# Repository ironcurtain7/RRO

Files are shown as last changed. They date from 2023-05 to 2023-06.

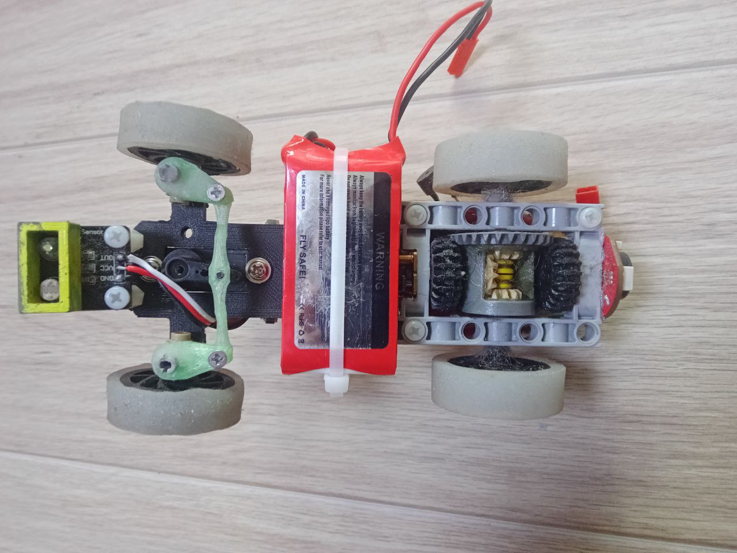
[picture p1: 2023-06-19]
v-photos/5.jpg

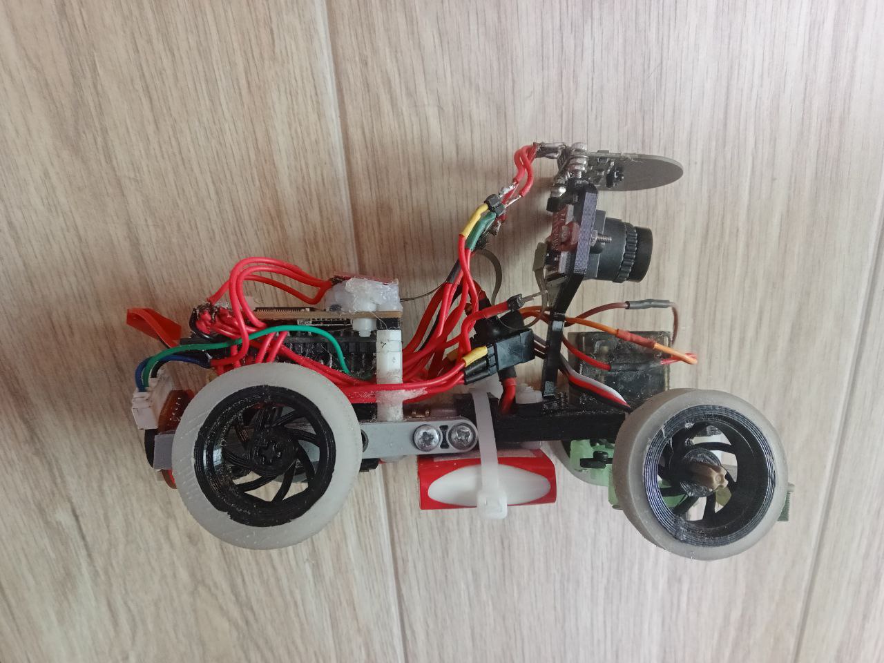
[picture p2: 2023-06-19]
v-photos/3.jpg

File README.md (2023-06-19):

Команда Роботикс (Robotx). Описание робота для соревновний FutureEngineers 2023.

Файловая структура:

models - модели для 3d печати.

t-photos - фото команды.

v-photos - фото транспортного средства.

schemes - схема электронных компонентов.

src - исходный код программ.

Робот был сделан на основе самостоятельно разработанного и напечатанного на 3D-принтере шасси, а так же элементов LEGO. 3D модели для печати находятся в папке models. Вариант самостоятельной разработки шасси был выбран по двум причинам:

- возможность сделать шасси нужной конфигурации для оптимального расположения электронных и механических компонентов робота
- уменьшения массы робота и улучшенния маневренности по сравнению с готовыми радиоуправляемыми шасси
  
Система перемещения робота:

Автомобиль состоит из: двусоставной рамы(из напечатанных деталей и частей конструктора LEGO, крепления мотора, крепления камеры, крепления датчиков, дисков колес и силиконовых покрышек.(car_frame.stl, motor_mount.stl, camera_mount.stl, sensor_mount.stl, rim.stl, wheels1.stl, wheels2.stl)

Электронная составляющая робота: ESP32(главный микроконтроллер), OpenMV H7(второстепенный контроллер для обработки изображения с камеры), стабилизатор напряжения mini360, двигатель MR12-020, драйвер двигателя ta6586, инфракрасный дальномер OPT3101, сервопривод Tower Pro MG90S, а питание идет от аккамулятора LiPo 2s (7.4V) 460mAh.

Используемые датчики: Инфракрасный дальномер OPT3101 (для определения расстояния до стены), фоторезистор со светодиодной подсветкой (для определения цвета линий).

Подключение всех электронных эллементов происходит через провода в силиконовой оболочке т. к. пайка дает лучше соеденение чем стандартные коннекторы.

Для крепления компонентов много где используются пластиковые стойки и пластиковые винты с гайками.

Робот включается с помощью выключателя на кабеле к батарее. Запускаются оба контроллера. После этого ESP32 инициализирует драйвер/основной двигатель, сервопривод, датчик расстояния и датчик линии. После этого издается звуковой сигнал и робот ждет нажатия на кнопку старта.

Логика работы программы:

Квалификационный заезд (робот устанавливается на поле строго вдоль бортов, основная программа начинает работать после нажатия кнопки старта):

1. Робот двигается вперед строго прямо до нахождения синей/оранжевой полосы с помощью датчика яркости света
2. Если найдена синяя/оранжевая полоса, то в зависимости от цвета линии, робот едет с поворотом колес налево/направо на нужный угол необходимое количество времени таким образом, чтобы подъехать к перпендикулярной стене на расстояние примерно 20см и встать вдоль нее. Угол и время проезда подбирается опытным путем.
3. Затем запускается блок программы езды вдоль внешней стены полигона с помощью дальномеров и PID-регулятора. Робот едет на расстоянии 20см от внешней стены. Т.е. если первый поворот был налево и внешняя стенка справа, то едем по правому дальномеру. И наоборот.
4. Во время езды вдоль стены анализируем показания датчика яркости и определяем наезд на синюю/оранжевую линию.
5. Если наехали на синюю/оранжевую линию, то робот поворачивает колеса на нужный угол налево/направо и проезжает неободимое расстояние для того, чтобы подъехать к перпендикулярной стене на расстояние 20см и встать вдоль нее. Угол и расстояние проезда подбирается опытным путем.
Затем алгоритм повторяется с п.3 до тех пор пока количество поворотов не достигнет 12.
После проезда двенадцатого поворота проезжаем заранее подобранное время с заранее подобранным углом поворота колес и останавливаемся.

Финальный заезд (робот устанавливается на поле строго вдоль бортов, основная программа начинает работать после нажатия кнопки старта):

1. Двигается вперед строго прямо до нахождения синей/оранжевой полосы с помощью датчика яркости света. Если перед роботом стоит кубик, то объезжаем его(алгоритм объезда описан в п.3).
2. Если найдена синяя/оранжевая полоса, то в зависимости от цвета линии, робот едет с поворотом колес налево/направо на нужный угол необходимое количество времени таким образом, чтобы подъехать к перпендикулярной стене на расстояние примерно 50см и встать вдоль нее. Угол и время проезда подбирается опытным путем.
3. Затем запускается блок программы езды вдоль внешней стены полигона с помощью дальномеров и PID-регулятора. Робот едет на расстоянии 50см от внешней стены. Т.е. если первый поворот был налево и внешняя стенка справа, то едем по правому дальномеру. И наоборот.
Во время езды вдоль стены анализируем показания с контроллера OpenMV H7. Если контроллер OpenMV находит препятствие, то передает данные о цвете и координатах препятствия на контроллер ESP32. ESP32 направляет робота на препятсвие (постоянно получая данные с OpenMV о координатах препятсвия) для того, чтобы выровнять робота относительно препятствия. Т.е. препятсвие будет находиться строго перед роботом. Далее робот делает маневр объезда препятсвия в зависимости от цвета слева или справа. Объезд (углы поворота колес и время проезда) настраивается опытным путем. После объезда робот снова начинает ехать вдоль внешней стены.
4. Одновременно с получением данных с OpenMV, контроллер ESP32 анализирует показания датчика яркости и определяет наезд на синюю/оранжевую линию.
5. Если наехали на синюю/оранжевую линию, то робот поворачивает колеса на нужный угол налево/направо и проезжает неободимое расстояние для того, чтобы подъехать к перпендикулярной стене на расстояние 20см и встать вдоль нее. Угол и расстояние проезда подбирается опытным путем.
Затем алгоритм повторяется с п.3 до тех пор пока количество поворотов не достигнет 12.
После проезда двенадцатого поворота проезжаем заранее подобранное время с заранее подобранным углом поворота колес и останавливаемся.

Программа для ESP32 написана на языке C++, для OpenMV - на языке python. Исходный код находится в папке src.

qual.cpp - программа для квалификационного заезда на ESP32

final.cpp - программа для финального заезда на ESP32

main.py - программа для контроллера OpenMV H7

Программы для ESP32 используют стандартные библиотеки из фреймворка PlatformIO, компилируются и загружаются в контроллер в среде Microsoft Visual Studio Code. Программа для OpenMV H7 загружается в контроллер с помощью стандартной среды разработки от контроллеров OpenMV. (Скачать можно по ссылке https://openmv.io/pages/download)

Программы для квалификационного и финального заездов во многом схожи и состоят из таких блоков:

Блок добавления библиотек, определения переменных и создание объектов для управления сервоприводом, основным двигателем и дальномерами.

Функция Setup(). Инициализация дальномеров. Указание его режима и параметров работы, а так же инициализация Serial порта, драйвера, сервопривода, датчика линии и т.д.

Функция start(). Проезд до первого поворота, определение направления поворота и непосредственно выполнение поворота.

Функция speek(). Отладочная функция которая издает звуковые сигналы в зависимости от выбранного времени звучания при помощи входного параметра функции

Функция ReadUZ(). Считывание расстояние с датчика в зависимости от выбранного датчика при помощи входного параметра функции(возвращает растояние до стены, и используется в функциях ride(), turn())

Функция ride(). Езда вдоль стены с заданным расстоянием. В программе final.cpp в данной функции еще и объезд светофоров в зависимости от цвета слева/справа.

Функция turn(). Поворот под прямым углом в зависимости от цвета линии налево/направо.

Функция loop(). Основной цикл программы. В ней вызываются функции для езды робота.

В программе для контроллера OpenMV H7 следующие блоки:

Импорт библиотек и определение переменных

Определение порогов цветов в цветовой модели LAB для определения объектов красного и зеленого цветов.

Настройка Serial порта и режима работы камеры

Блок определения красных объектов в необходимой области видимости (ROI) и передача цвета и х-координаты и высоты светофора в контроллер ESP32 по Serial порту.
Блок определения зеленых объектов в необходимой области видимости (ROI) и передача цвета и х-координаты и высоты светофора в контроллер ESP32 по Serial порту.

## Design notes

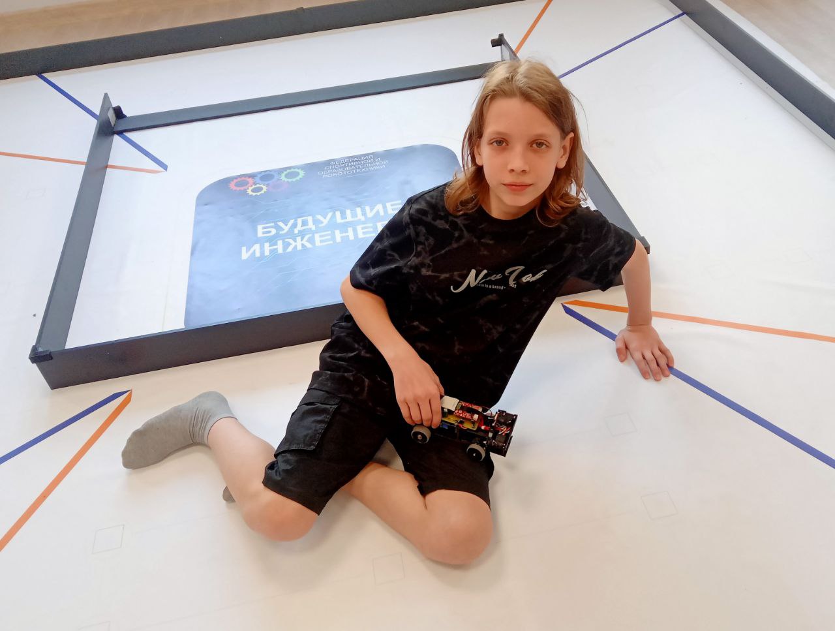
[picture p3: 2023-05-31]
t-photos/funny.jpg

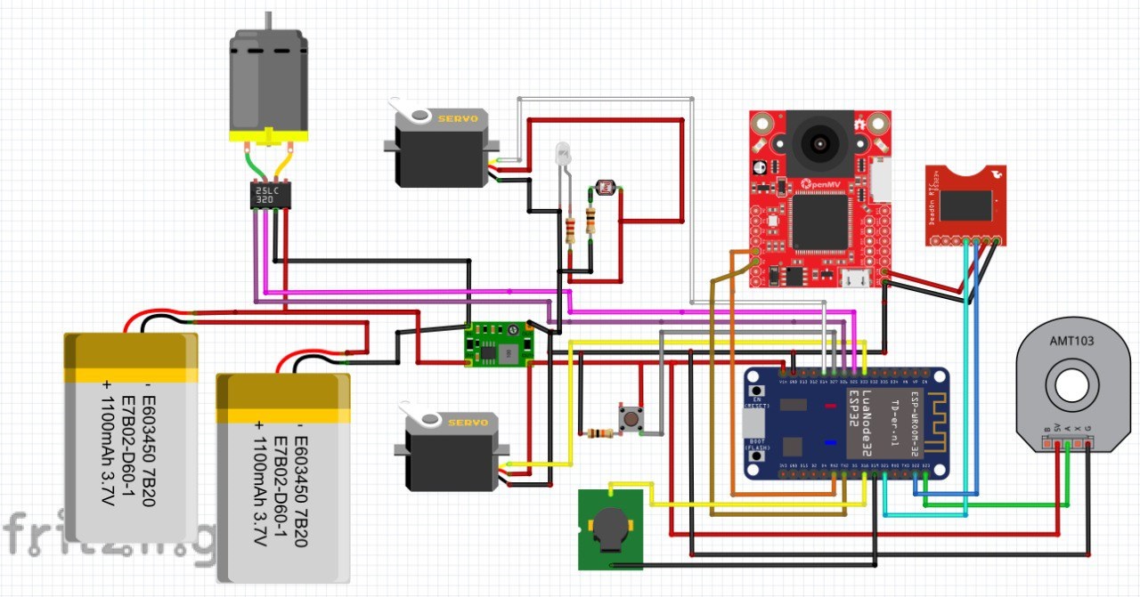
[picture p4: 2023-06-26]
schemes/image.jpg

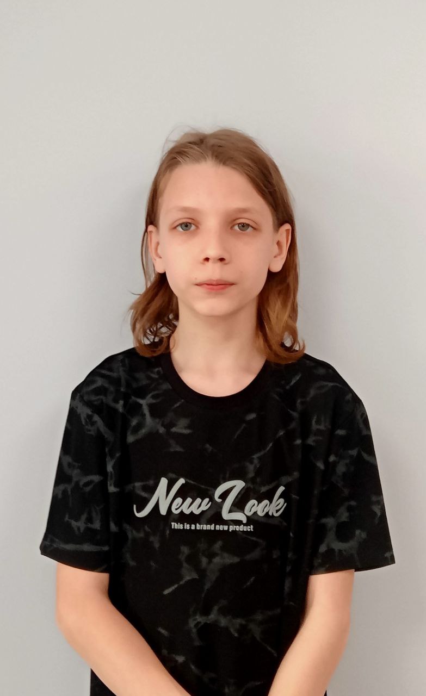
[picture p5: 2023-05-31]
t-photos/official.jpg

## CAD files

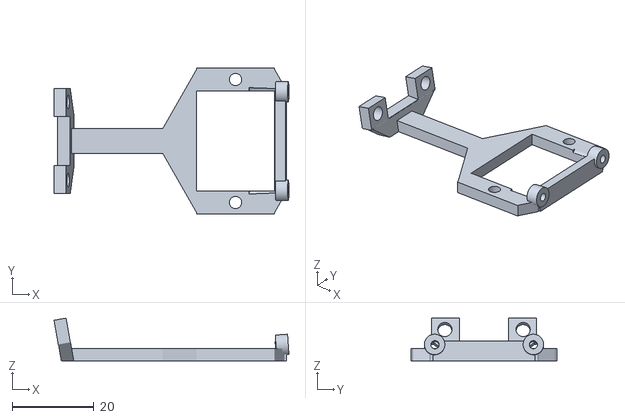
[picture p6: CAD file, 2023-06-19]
models/camera_and_sensor_stand.stl
57.3 x 35.5 x 10.4

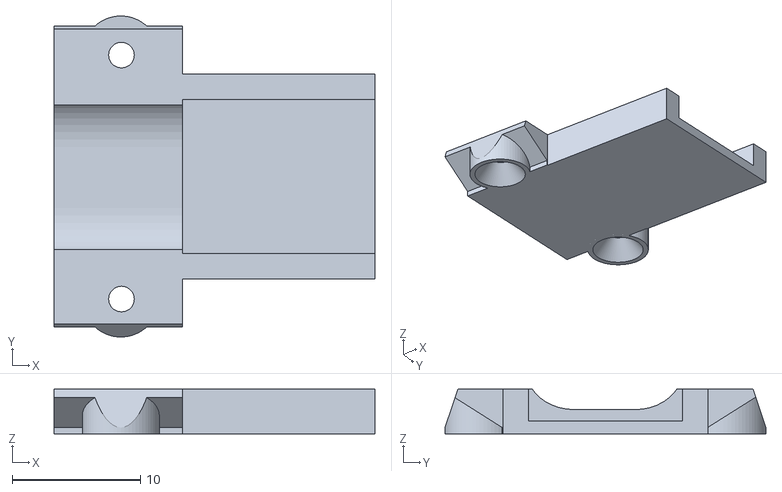
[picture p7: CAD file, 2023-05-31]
models/motor_cover.stl
25.0 x 25.0 x 3.50

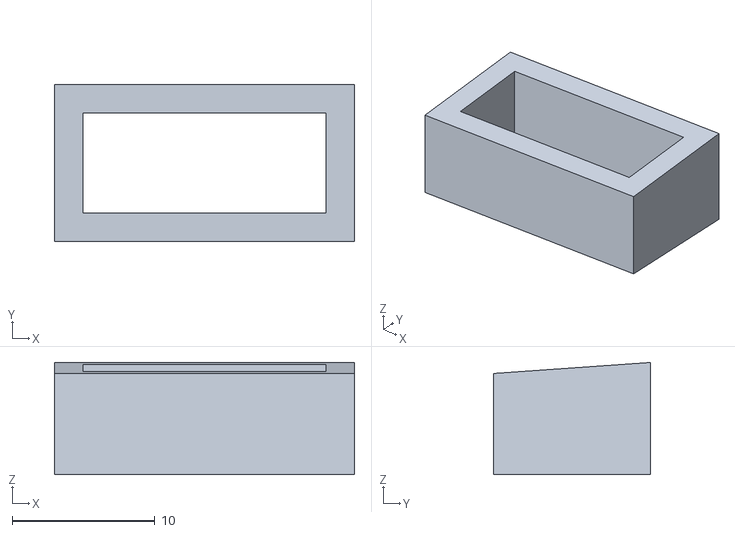
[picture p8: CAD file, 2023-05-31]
models/sensor_shutter.stl
21.0 x 11.0 x 7.84

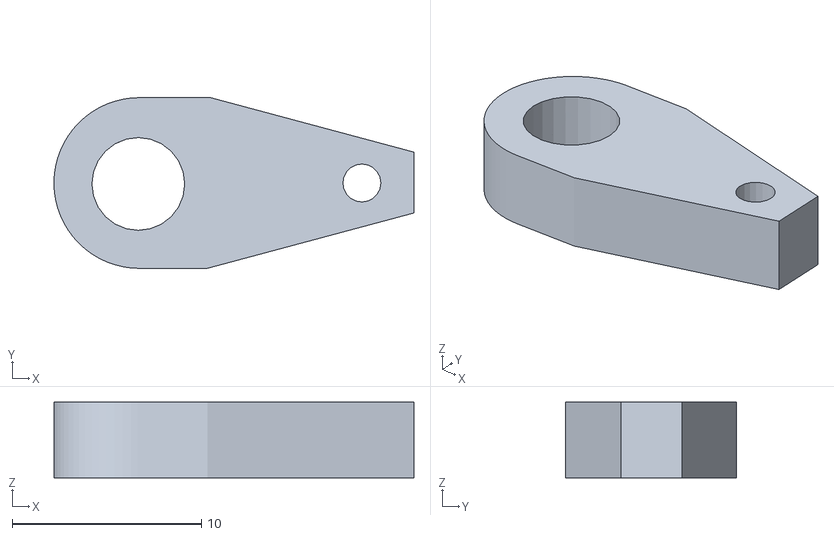
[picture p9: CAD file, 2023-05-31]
models/steering_fist.stl
19.0 x 9.00 x 4.00

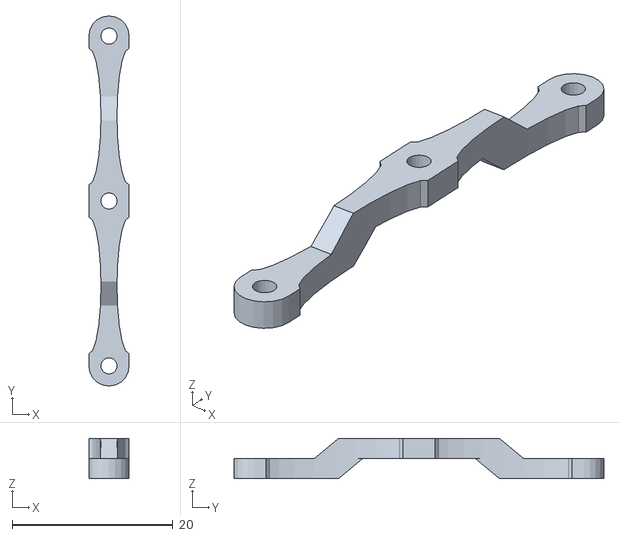
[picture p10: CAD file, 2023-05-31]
models/steering_rod.stl
5.00 x 46.0 x 5.00

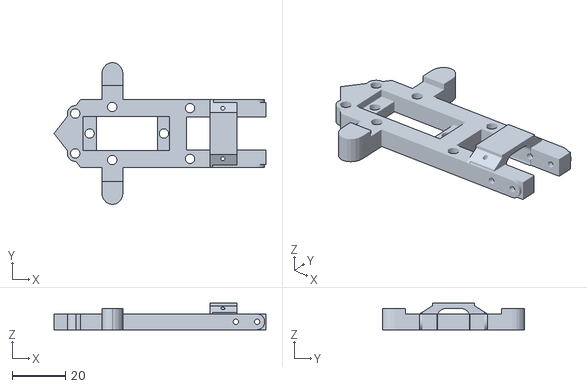
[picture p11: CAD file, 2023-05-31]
models/car_frame.stl
79.8 x 53.5 x 10.00

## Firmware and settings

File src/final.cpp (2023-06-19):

#include <Arduino.h>
#include <Servo.h>
#include <WiFi.h>
#include <AsyncTCP.h>
#include <ESPAsyncWebServer.h>
#include <OPT3101.h>
#include <Wire.h>
#include "BasicOTA.hpp"
int flagcube = 1;
int cx = 0, ch = 0, iwhile = 0, iexit = 0, els = 0, I;
long readsens;
int error, color, delta = 0, flag5 = 0;
int dist = 500, errorold = 0, i = 0, speedwhile = 0;
int LigR, sum, count, timold = 0, countline = 0;
#define SSID      "DIR-615-effb"
#define PASSWORD  "18050523"
#define RXD2 16
#define TXD2 17
float Kp = 0.065, Ki = 0.01, Kd = 0.05;
int white = 3420;
int blue = 3270;
int timing = 52;
int speed = 70;
int tim1 = 0, tim2 = 0, tim3 = 0, ang1 = 25, ang2 = 25, ang3 = 50;
  int speed1 = speed;
String Kp_text = String(Kp, 5);
String Ki_text = String(Ki, 5);
String Kd_text = String(Kd, 5);
String white_text = String(white);
String blue_text = String(blue);
String speed_text = String(speed);
String timing_text = String(timing);

String tim1_text = String(tim1);
String tim2_text = String(tim2);
String tim3_text = String(tim3);

String ang1_text = String(ang1);
String ang2_text = String(ang2);
String ang3_text = String(ang3);
uint16_t amplitudes[3];
int16_t distances[3];
AsyncWebServer server(80);
Servo servo1;
OPT3101 sensor;
BasicOTA OTA;
TaskHandle_t Task1;

int readUZ(int LR){


if (LR ==  0){ // LEFT


if (sensor.isSampleDone())
  {
    sensor.readOutputRegs();

    amplitudes[sensor.channelUsed] = sensor.amplitude;
    distances[sensor.channelUsed] = sensor.distanceMillimeters;
    sensor.nextChannel();
    sensor.startSample();
    dist = distances[0];
  }
}
if (LR == 1){ // right

if (sensor.isSampleDone())
  {
    sensor.readOutputRegs();

    amplitudes[sensor.channelUsed] = sensor.amplitude;
    distances[sensor.channelUsed] = sensor.distanceMillimeters;
    sensor.nextChannel();
    sensor.startSample();
    dist = distances[2];
  }

}
if (LR ==  2){ // CENTER


if (sensor.isSampleDone())
  {
    sensor.readOutputRegs();

    amplitudes[sensor.channelUsed] = sensor.amplitude;
    distances[sensor.channelUsed] = sensor.distanceMillimeters;
    sensor.nextChannel();
    sensor.startSample();
    dist = distances[1];
  }
}

return dist;


}

void speek(int variation){
if (variation == 0){
digitalWrite(14,HIGH);
delay(50);
digitalWrite(14,LOW);
}
if (variation == 1){
digitalWrite(14,HIGH);
delay(500);
digitalWrite(14,LOW);
}
if (variation == -1){
digitalWrite(14,HIGH);
delay(10);
digitalWrite(14,LOW);
}
}

void Task1code( void * pvParameters ){

int timold1 = 0, LigR1 = 0, sum1, i1;
while (1){

LigR1=analogRead(32);
sum1 = 0;
if (LigR1<white){
  for (i1 = 0; i1 < 10; i1++) {
    LigR1=analogRead(32);
    sum1 = sum1 + LigR1;
  }

if (sum1/i1<white){
  if (millis() - timold1 > 3000){
    speek(1);
    timold1 = millis();

    countline = countline + 1;
}
    
}

}




} 
}

void arc(int speed, int dir, int angle){
int count1 = 0;

if (dir == 0){
digitalWrite(25, LOW);
analogWrite(26,speed);
}
if (dir == -1){
digitalWrite(25, HIGH);
analogWrite(26, 255-speed);
}

while (count1 < angle){
if (digitalRead(23) == 1){
while (digitalRead(23) == 1){}
count1 = count1 + 1;
}
}


}

void ride(){
cx = 0, ch = 0, iwhile = 0, iexit = 0, els = 0, I = 0;
digitalWrite(25, LOW);
analogWrite(26,speed);


  if (Serial2.available() > 0){
    String rd = Serial2.readStringUntil('\n');
    if (rd[0] == 'r'){
      if (flagcube == 1){
      while(iexit == 0){
        delay(3);
        if (Serial2.available() > 0){

          String rd = Serial2.readStringUntil('\n');
          String rc = rd.substring(1,4);
          String rh = rd.substring(4,6); 
          cx = rc.toInt();
          ch = rh.toInt();
          
          }
          
          

      int err = 20 - cx;
      int u1 = err * 0.5;
      //Serial.println(u1);
      servo1.write(80 - u1);      

      if (ch > 65) iexit = 1;

      }
      servo1.write(107);
      arc(70,0,20);
      servo1.write(67);
      arc(70,0,15);
      while (Serial2.available()) Serial2.read();

      }

    }// (rd[0] == 'r')

    else if (rd[0] == 'g'){
      if (flagcube == 1){

      while(iexit == 0){
        delay(3);
        if (Serial2.available() > 0){

          String rd = Serial2.readStringUntil('\n');
          String rc = rd.substring(1,4);
          String rh = rd.substring(4,6); 
          cx = rc.toInt();
          ch = rh.toInt();
          
          }
          
          

      int err = 100 - cx;
      int u1 = err * 0.5;
      //Serial.println(u1);
      servo1.write(87 - u1);      

      if (ch > 55) iexit = 1;

      }
      servo1.write(55);
      arc(70,0,20);
      servo1.write(115);
      arc(70,0,18);
      while (Serial2.available()) Serial2.read();


      }
    }// (rd[0] == 'g')
  }
    else {
      analogWrite(26,speed);


      readsens = readUZ(1-color);
      Serial.println(readsens);
      error = (readsens - 1200) * (color * 2 - 1) - cx * 5;



      I = I + error;
      int u = error * Kp + Kd * (error - errorold) + Ki * I;
      errorold = error;


      if (u>ang3){
      u = ang3;
      }

      if (u<ang3*-1){
        u = ang3*-1;
      }
      if (flag5 == 0){
        servo1.write(87-u);
      }

      }// (rd[0] == 'n')

          
      





}

void turn(){




LigR=analogRead(32);



sum=0;
if (LigR<white){
  for (i = 0; i < 10; i++) {
    LigR=analogRead(32);
    sum = sum + LigR;
  }

if (sum/i<white){
  if (millis() - timold > 3000){
    digitalWrite(25, LOW);
analogWrite(26,0);
delay(1000);
digitalWrite(25, LOW);
analogWrite(26,speed);
    //speek(0);
    if (color == 0){
    servo1.write(87);
    while (readUZ(2) > 250){}
    servo1.write(120);
    arc(80,-1,timing);
    servo1.write(87);
    arc(80,-1,20);
    }
    else{
    servo1.write(87);
    while (readUZ(2) > 250){}
    servo1.write(60);
    arc(80,-1,timing);
    servo1.write(87);
    arc(80,-1,20);
    }
    timold = millis();
digitalWrite(25, LOW);
analogWrite(26,0);
delay(1000);
digitalWrite(25, LOW);
analogWrite(26,speed);
    count = count + 1;
}
    
}

}

while (Serial2.available()) Serial2.read();


if (count == 111){
  int mil = millis();
while(millis() - mil < 750){
  ride();
}
digitalWrite(25, LOW);
analogWrite(26,0);
speek(1);
speek(1);
delay(10000000);
}
servo1.write(87);







}

void start(){

cx = 0, ch = 0, iwhile = 0, iexit = 0, els = 0;
int porog, flag = 0, Min = 9999;

while (Serial2.available()) Serial2.read();

digitalWrite(25, LOW);
analogWrite(26,speed);




while (flag == 0){

servo1.write(86);

if (Serial2.available() > 0){
    String rd = Serial2.readStringUntil('\n');
    if (rd[0] == 'r'){
      
      while(iexit == 0){
        delay(3);
        if (Serial2.available() > 0){

          String rd = Serial2.readStringUntil('\n');
          String rc = rd.substring(1,4);
          String rh = rd.substring(4,6); 
          cx = rc.toInt();
          ch = rh.toInt();
          
          }
          
          

      int err = 20 - cx;
      int u1 = err * 0.5;
      //Serial.println(u1);
      servo1.write(80 - u1);      

      if (ch > 65) iexit = 1;

      }
      servo1.write(107);
      arc(70,0,20);
      servo1.write(67);
      arc(70,0,15);
      while (Serial2.available()) Serial2.read();



    }// (rd[0] == 'r')

    if (rd[0] == 'g'){


      while(iexit == 0){
        delay(3);
        if (Serial2.available() > 0){

          String rd = Serial2.readStringUntil('\n');
          String rc = rd.substring(1,4);
          String rh = rd.substring(4,6); 
          cx = rc.toInt();
          ch = rh.toInt();
          
          }
          
          

      int err = 100 - cx;
      int u1 = err * 0.5;
      //Serial.println(u1);
      servo1.write(87 - u1);      

      if (ch > 60) iexit = 1;

      }
      servo1.write(62);
      arc(70,0,20);
      servo1.write(112);
      arc(70,0,15);
      while (Serial2.available()) Serial2.read();



    }// (rd[0] == 'g')
}

LigR=analogRead(32);
//Serial.print(LigR);
//Serial.print("                        ");
sum=0;

if (LigR<white){
  for (i = 0; i < 10; i++) {
    LigR=analogRead(32);
    sum = sum + LigR;
  }

porog = sum/i;
Serial.println(porog);
if (porog<white){
flag = 1;
while (porog<white){


LigR=analogRead(32);
//Serial.print(LigR);
//Serial.print("                        ");
sum=0;

  for (i = 0; i < 10; i++) {
    LigR=analogRead(32);
    sum = sum + LigR;
  }

porog = sum/i;


  if (porog<Min){
    Min = porog;
  } 
}   
}
}
}





Serial.println(Min);

if (Min > blue){
  color = 1;
Serial.print("ORANGE");
servo1.write(87);
    arc(70,0,70);
    servo1.write(60);
    arc(70,-1,timing);


}
else{
  color = 0;
Serial.print("BLUE");
servo1.write(87);
    arc(70,0,70);
    servo1.write(120);
    arc(70,-1,timing);



}

timold = millis();
speek(0);
while (Serial2.available()) Serial2.read();
}

void notFound(AsyncWebServerRequest *request) {
  request->send(404, "text/plain", "Not found");
}

void IRAM_ATTR push_button() {

if (speed>0)
speed = 0;
else
speed = speed1;

delay(350);
}

void setup() {
pinMode(25, OUTPUT); // configure the trigger_pin(D9) as an Output
pinMode(26, OUTPUT); // Set the LED (D13) pin as a digital output
pinMode(14, OUTPUT); // configure the trigger_pin(D9) as an Output
pinMode(27, INPUT_PULLUP);
Serial.begin(115200); // Enable the serial with 9600 baud rate
Serial2.begin(115200, SERIAL_8N1, RXD2, TXD2);

Wire.begin();

servo1.attach(33);
servo1.write(87);




  sensor.init();
  if (sensor.getLastError())
  {
    Serial.print(F("Failed to initialize OPT3101: error "));
    Serial.println(sensor.getLastError());
    while (1) {}
  }

  sensor.setFrameTiming(64);
  sensor.setChannel(0);
  sensor.setBrightness(OPT3101Brightness::High);

  sensor.startSample();







//WiFi.mode(WIFI_AP);
//WiFi.softAP("ESP32AP","123321456");




  Serial.println("Startup");
  WiFi.mode(WIFI_STA);
  WiFi.begin(SSID, PASSWORD);
  while (WiFi.waitForConnectResult() != WL_CONNECTED) {
    Serial.println("Connection Failed! Rebooting...");
    delay(5000);
    ESP.restart();
  }

  OTA.begin(); // Setup settings

  Serial.println("Ready");
  Serial.print("IP address: ");
  Serial.println(WiFi.localIP());

  // Send web page with input fields to client
  server.on("/", HTTP_GET, [](AsyncWebServerRequest *request){

String mess = "<!DOCTYPE HTML><html><head><title>ESP Input \
    Form</title><meta name='viewport' content='width=device-width, initial-scale=1'></head><body><form action='/get'> \
    kP: <input type='text' name='Kp' value='"+Kp_text+"'><br> \
    kI: <input type='text' name='Ki' value='"+Ki_text+"'> \
    <br>kD: <input type='text' name='Kd' value='"+Kd_text+"'>\
    <br>speed: <input type='text' name='speed' value='"+speed_text+"'>\
    <br>white: <input type='text' name='white' value='"+white_text+"'>\
    <br>blue: <input type='blue' name='blue' value='"+blue_text+"'>\
    <br>timing: <input type='timing' name='timing' value='"+timing_text+"'>\
    <br>tim1: <input type='tim1' name='tim1' value='"+tim1_text+"'>\
    <br>ang1: <input type='ang1' name='ang1' value='"+ang1_text+"'>\
    <br>tim2: <input type='tim2' name='tim2' value='"+tim2_text+"'>\
    <br>ang2: <input type='ang2' name='ang2' value='"+ang2_text+"'>\
    <br>tim3: <input type='tim3' name='tim3' value='"+tim3_text+"'>\
    <br>ang3: <input type='ang3' name='ang3' value='"+ang3_text+"'>\
    <input type='submit' value='Submit'>\
  </form>\
</body></html>";
    
    request->send(200, "text/html", mess);

});

  // Send a GET request to <ESP_IP>/get?input1=<inputMessage>
  server.on("/get", HTTP_GET, [] (AsyncWebServerRequest *request) {
    String inputMessage;
    String inputParam;
    // GET input1 value on <ESP_IP>/get?input1=<inputMessage>
    if (request->hasParam("Kp")) {
      Kp_text = request->getParam("Kp")->value();
    }
    // GET input2 value on <ESP_IP>/get?input2=<inputMessage>
    if (request->hasParam("Ki")) {
      Ki_text = request->getParam("Ki")->value();
    }
    // GET input3 value on <ESP_IP>/get?input3=<inputMessage>
    if (request->hasParam("Kd")) {
      Kd_text = request->getParam("Kd")->value();
    }

    if (request->hasParam("speed")) {
      speed_text = request->getParam("speed")->value();
    }
    
    if (request->hasParam("white")) {
      white_text = request->getParam("white")->value();
    }

    if (request->hasParam("blue")) {
      blue_text = request->getParam("blue")->value();
    }

    if (request->hasParam("timing")) {
      timing_text = request->getParam("timing")->value();
    }
    if (request->hasParam("tim1")) {
      tim1_text = request->getParam("tim1")->value();
    }
    if (request->hasParam("tim2")) {
      tim2_text = request->getParam("tim2")->value();
    }
    if (request->hasParam("tim3")) {
      tim3_text = request->getParam("tim3")->value();
    }
    if (request->hasParam("ang1")) {
      ang1_text = request->getParam("ang1")->value();
    }
    if (request->hasParam("ang2")) {
      ang2_text = request->getParam("ang2")->value();
    }
    if (request->hasParam("ang3")) {
      ang3_text = request->getParam("ang3")->value();
    }



    Kp = Kp_text.toFloat();
    Ki = Ki_text.toFloat();
    Kd = Kd_text.toFloat();
    speed = speed_text.toInt();
    white = white_text.toInt();
    blue = blue_text.toInt();
    timing = timing_text.toInt();
    tim1 = tim1_text.toInt();
    tim3 = tim2_text.toInt();
    tim1 = tim3_text.toInt();
    ang1 = ang1_text.toInt();
    ang2 = ang2_text.toInt();
    ang3 = ang3_text.toInt();

    Serial.println(String(Kp,5));
    Serial.println(String(Ki,5));
    Serial.println(String(Kd,5));


int light = 0;
 sum = 0;
for (i = 0; i < 10; i++) {
    LigR=analogRead(32);
    sum = sum + LigR;
  }
light = sum/i;

int rightread = -1;
int leftread = -1;
Serial.println(rightread);
Serial.println(leftread);
String light_text = String(light);
String right_dist = String(rightread);
String left_dist = String(leftread);

String count_text=String(count);

String mess = "<!DOCTYPE HTML><html><head><title>ESP Input \
    Form</title><meta name='viewport' content='width=device-width, initial-scale=1'></head><body> \
    Kp="+Kp_text+"  Ki="+Ki_text+"  Kd="+Kd_text+"  Light="+light_text+"  Right_dist="+right_dist+"  Left_dist="+left_dist+"  Count="+count_text+" \
    <form action='/get'> \
    kP: <input type='text' name='Kp' value='"+Kp_text+"'><br> \
    kI: <input type='text' name='Ki' value='"+Ki_text+"'> \
    <br>kD: <input type='text' name='Kd' value='"+Kd_text+"'>\
    <br>speed: <input type='text' name='speed' value='"+speed_text+"'>\
    <br>white: <input type='text' name='white' value='"+white_text+"'>\
    <br>blue: <input type='blue' name='blue' value='"+blue_text+"'>\
    <br>timing: <input type='timing' name='timing' value='"+timing_text+"'>\
    <br>tim1: <input type='tim1' name='tim1' value='"+tim1_text+"'>\
    <br>ang1: <input type='ang1' name='ang1' value='"+ang1_text+"'>\
    <br>tim2: <input type='tim2' name='tim2' value='"+tim2_text+"'>\
    <br>ang2: <input type='ang2' name='ang2' value='"+ang2_text+"'>\
    <br>tim3: <input type='tim3' name='tim3' value='"+tim3_text+"'>\
    <br>ang3: <input type='ang3' name='ang3' value='"+ang3_text+"'>\
    <input type='submit' value='Submit'>\
  </form>\
</body></html>";

    request->send(200, "text/html", mess);
  });
  server.onNotFound(notFound);
  server.begin();

speek(1);
while (digitalRead(27) == 0){
OTA.handle();
}
Serial.println("START ROBOT");



start();

xTaskCreatePinnedToCore(Task1code, "Task1", 10000, NULL, 1, &Task1, 1); // надо 
attachInterrupt(27, push_button, RISING);
}

void loop() {

ride();
turn();
}

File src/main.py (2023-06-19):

# Single Color RGB565 Blob Tracking Example
#
# This example shows off single color RGB565 tracking using the OpenMV Cam.

import sensor, image, time, math, pyb
from pyb import UART
ledred = pyb.LED(1)
ledgreen = pyb.LED(2)
threshold_index = 0 # 0 for red, 1 for green, 2 for blue

# Color Tracking Thresholds (L Min, L Max, A Min, A Max, B Min, B Max)
# The below thresholds track in general red/green/blue things. You may wish to tune them...
thresholds = [(0, 85, -128, -7, -46, 47)] # green
thresholds1 = [(0, 86, 10, 104, 27, 127)] # red
#thresholds = [(0, 70, -92, -12, -15, 62)] # green
#thresholds1 = [(4, 69, 32, 120, -69, 117)  ] # red
uart = UART(3, 115200)
sensor.reset()
sensor.set_pixformat(sensor.RGB565)
sensor.set_framesize(sensor.QQVGA)
sensor.set_auto_gain(False) # must be turned off for color tracking
sensor.set_auto_whitebal(False) # must be turned off for color tracking
sensor.set_vflip(True)
sensor.set_hmirror(True)
#sensor.set_gainceiling()
#sensor.set_brightness(-3)
#sensor.set_contrast(-3)
#sensor.set_saturation(-3)
sensor.skip_frames(time = 2000)
clock = time.clock()
blob=0
# Only blobs that with more pixels than "pixel_threshold" and more area than "area_threshold" are
# returned by "find_blobs" below. Change "pixels_threshold" and "area_threshold" if you change the
# camera resolution. "merge=True" merges all overlapping blobs in the image.
cx=0
flag=0
while(True):
    flag=0
    clock.tick()
    img = sensor.snapshot()
    for blob in img.find_blobs(thresholds, roi=(0, 45, 160, 65), pixels_threshold=80, area_threshold=80, merge=True):

        # These values depend on the blob not being circular - otherwise they will be shaky.
        #if blob.rotation_deg() < 135 and blob.rotation_deg() > 45:

        img.draw_rectangle(blob.rect())
        img.draw_cross(blob.cx(), blob.cy())
        # Note - the blob rotation is unique to 0-180 only.
        #img.draw_keypoints([(blob.cx(), blob.cy(), int(math.degrees(blob.rotation())))], size=20)
        if blob.cx()>99:
            uart.write("g"+str(blob.cx()))
        if blob.cx()<100 and blob.cx()>9:
            uart.write("g0"+str(blob.cx()))
        if blob.cx()<10:
            uart.write("g00"+str(blob.cx()))
        if blob.h()<10:
            uart.write("0"+str(blob.h())+"\n")
        if blob.h()>9:
            uart.write(str(blob.h())+"\n")
        print("g")
        print(blob.h())
        ledgreen.on()
        flag=1




    for blob in img.find_blobs(thresholds1, roi=(0, 36, 160, 72), pixels_threshold=80, area_threshold=80, merge=False):
        #print(blob.rotation_deg())
        # These values depend on the blob not being circular - otherwise they will be shaky.
        if blob.rotation_deg() < 135 and blob.rotation_deg() > 45 and blob.elongation() < 0.8 and blob.density() > 0.6:
            # These values are stable all the time.
            img.draw_rectangle(blob.rect())
            img.draw_cross(blob.cx(), blob.cy())
            # Note - the blob rotation is unique to 0-180 only.
            #img.draw_keypoints([(blob.cx(), blob.cy(), int(math.degrees(blob.rotation())))], size=20)

            if blob.cx()>99:
                uart.write("r"+str(blob.cx()))
            if blob.cx()<100 and blob.cx()>9:
                uart.write("r0"+str(blob.cx()))
            if blob.cx()<10:
                uart.write("r00"+str(blob.cx()))
            if blob.h()<10:
                uart.write("0"+str(blob.h())+"\n")
            if blob.h()>9:
                uart.write(str(blob.h())+"\n")
            #print("r")
            print(blob.density())
            ledred.on()
            flag=1




    if flag==0:
        #print("999")
        ledred.off()
        ledgreen.off()


    #print(clock.fps())
